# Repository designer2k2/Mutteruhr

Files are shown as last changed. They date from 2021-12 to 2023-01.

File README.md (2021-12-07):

# Mutteruhr
a pulse of alternating polarity every minute.

Motherclock, or german "Mutteruhr" is a arduino based Master Clock or german "Hauptuhr". 
It generates a short pulse of alternating polarity to drive so called slave clocks or german "Nebenuhr".

https://en.wikipedia.org/wiki/Master_clock

With a DC/DC converter it uses minimal power, the highly accurate DS3231 RTC to keep time, and a Arduino Nano Every as a Brain.

grafik

grafik

## Circuit

Schematic: https://github.com/designer2k2/Mutteruhr/blob/main/MotherClock/Motherclock%20Schematic.pdf

The actual clock drive is a transistor h-bridge, parts can be either SMD or THT. 

2 Buttons and a DIL switch is on it to make settings while the clock operates.

A small mosfet can be used to switch some LED´s on/off

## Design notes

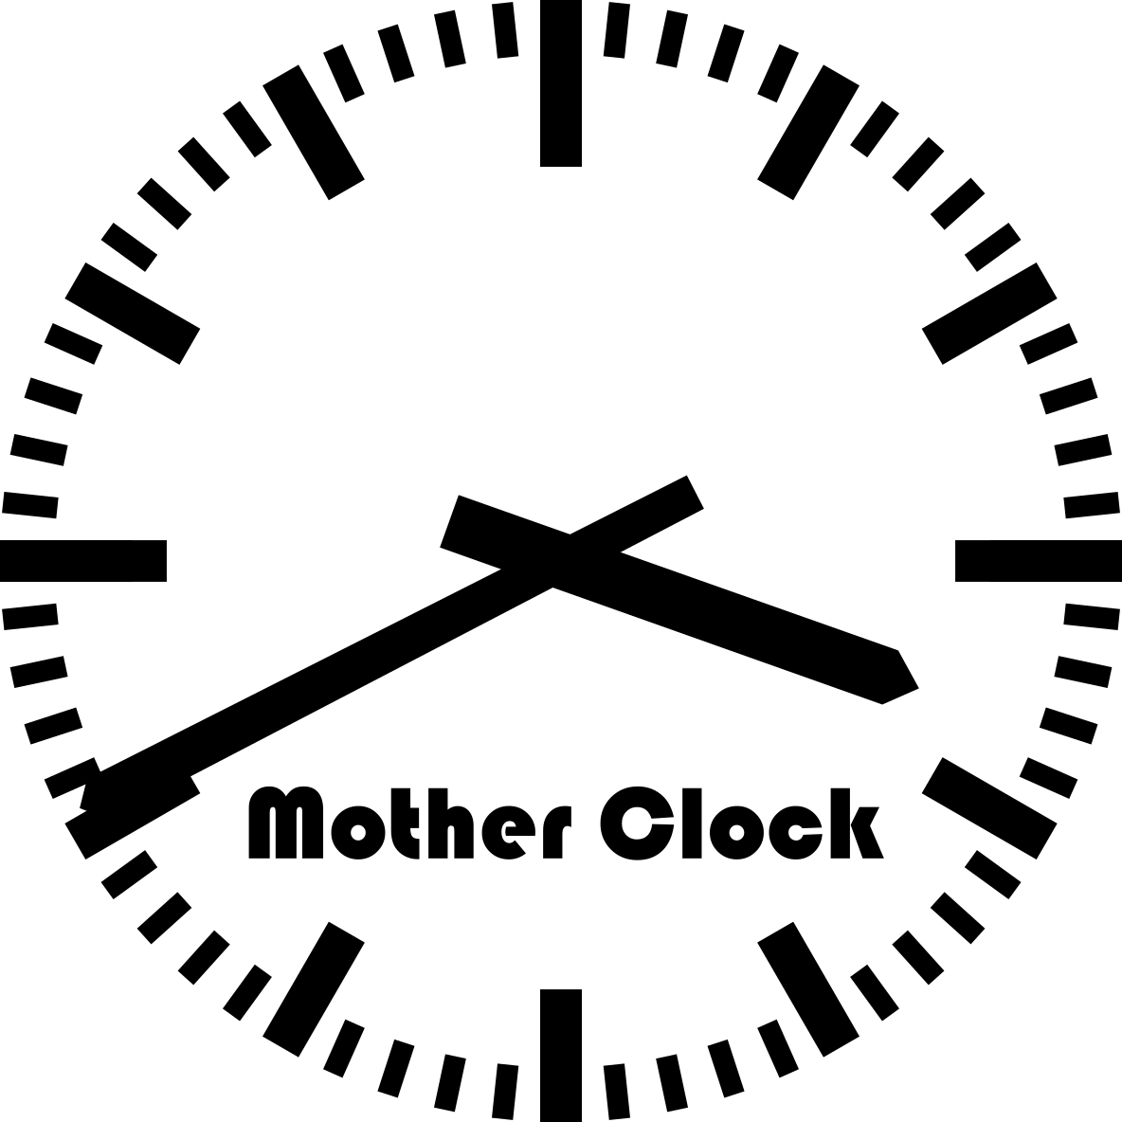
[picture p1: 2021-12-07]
MotherClock/MotherClock-brd.png

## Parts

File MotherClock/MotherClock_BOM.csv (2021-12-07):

Comment | Designator | Footprint | LCSC
Arduino_Nano_Every | A1 | Module:Arduino_Nano
1µ | C1 | Capacitor_THT:CP_Radial_D5.0mm_P2.00mm
2µ2 | C2 | Capacitor_THT:CP_Radial_D5.0mm_P2.00mm
22mF | C3 | Capacitor_THT:CP_Radial_D35.0mm_P10.00mm_SnapIn
C | C4 | Capacitor_THT:CP_Radial_D18.0mm_P7.50mm
100nF | C5,C6,C7 | Capacitor_SMD:C_0805_2012Metric
1N5818 | D1,D2,D3,D4,D6 | Diode_THT:D_DO-41_SOD81_P10.16mm_Horizontal
LED_Dual_2pin | D5 | LED_THT:LED_D3.0mm_Clear
SS15 | D7,D8,D9,D10,D11 | Diode_SMD:D_SMA
Main | J1 | TerminalBlock:TerminalBlock_Altech_AK300-4_P5.00mm
DS3231 Module | J2 | Connector_PinHeader_2.54mm:PinHeader_1x06_P2.54mm_Vertical
OLED | J3 | Connector_PinHeader_2.54mm:PinHeader_1x04_P2.54mm_Vertical
LED | J4 | TerminalBlock:TerminalBlock_Altech_AK300-2_P5.00mm
BC856 | Q1,Q3 | Package_TO_SOT_SMD:SOT-23
BC846 | Q2,Q4 | Package_TO_SOT_SMD:SOT-23
BC556 | Q5,Q7 | Package_TO_SOT_THT:TO-92_Inline_Wide
BC546 | Q6,Q8 | Package_TO_SOT_THT:TO-92_Inline_Wide
BS170 | Q9 | Package_TO_SOT_THT:TO-92_Inline
1k2 | R10 | Resistor_SMD:R_1206_3216Metric
47k | R11,R14 | Resistor_SMD:R_1206_3216Metric
10k | R12 | Resistor_SMD:R_1206_3216Metric
4k7 | R1,R2,R6,R9 | Resistor_SMD:R_1206_3216Metric
2k2 | R3,R7 | Resistor_SMD:R_1206_3216Metric
1k | R4,R5,R13 | Resistor_SMD:R_1206_3216Metric
1 | R8 | Resistor_SMD:R_1206_3216Metric
SW_DIP_x03 | SW1 | Button_Switch_THT:SW_DIP_SPSTx03_Slide_9.78x9.8mm_W7.62mm_P2.54mm
SW_Push | SW2,SW3 | Button_Switch_THT:SW_PUSH_6mm_H5mm
LM7805_TO220 | U1 | Package_TO_SOT_THT:TO-220-3_Vertical

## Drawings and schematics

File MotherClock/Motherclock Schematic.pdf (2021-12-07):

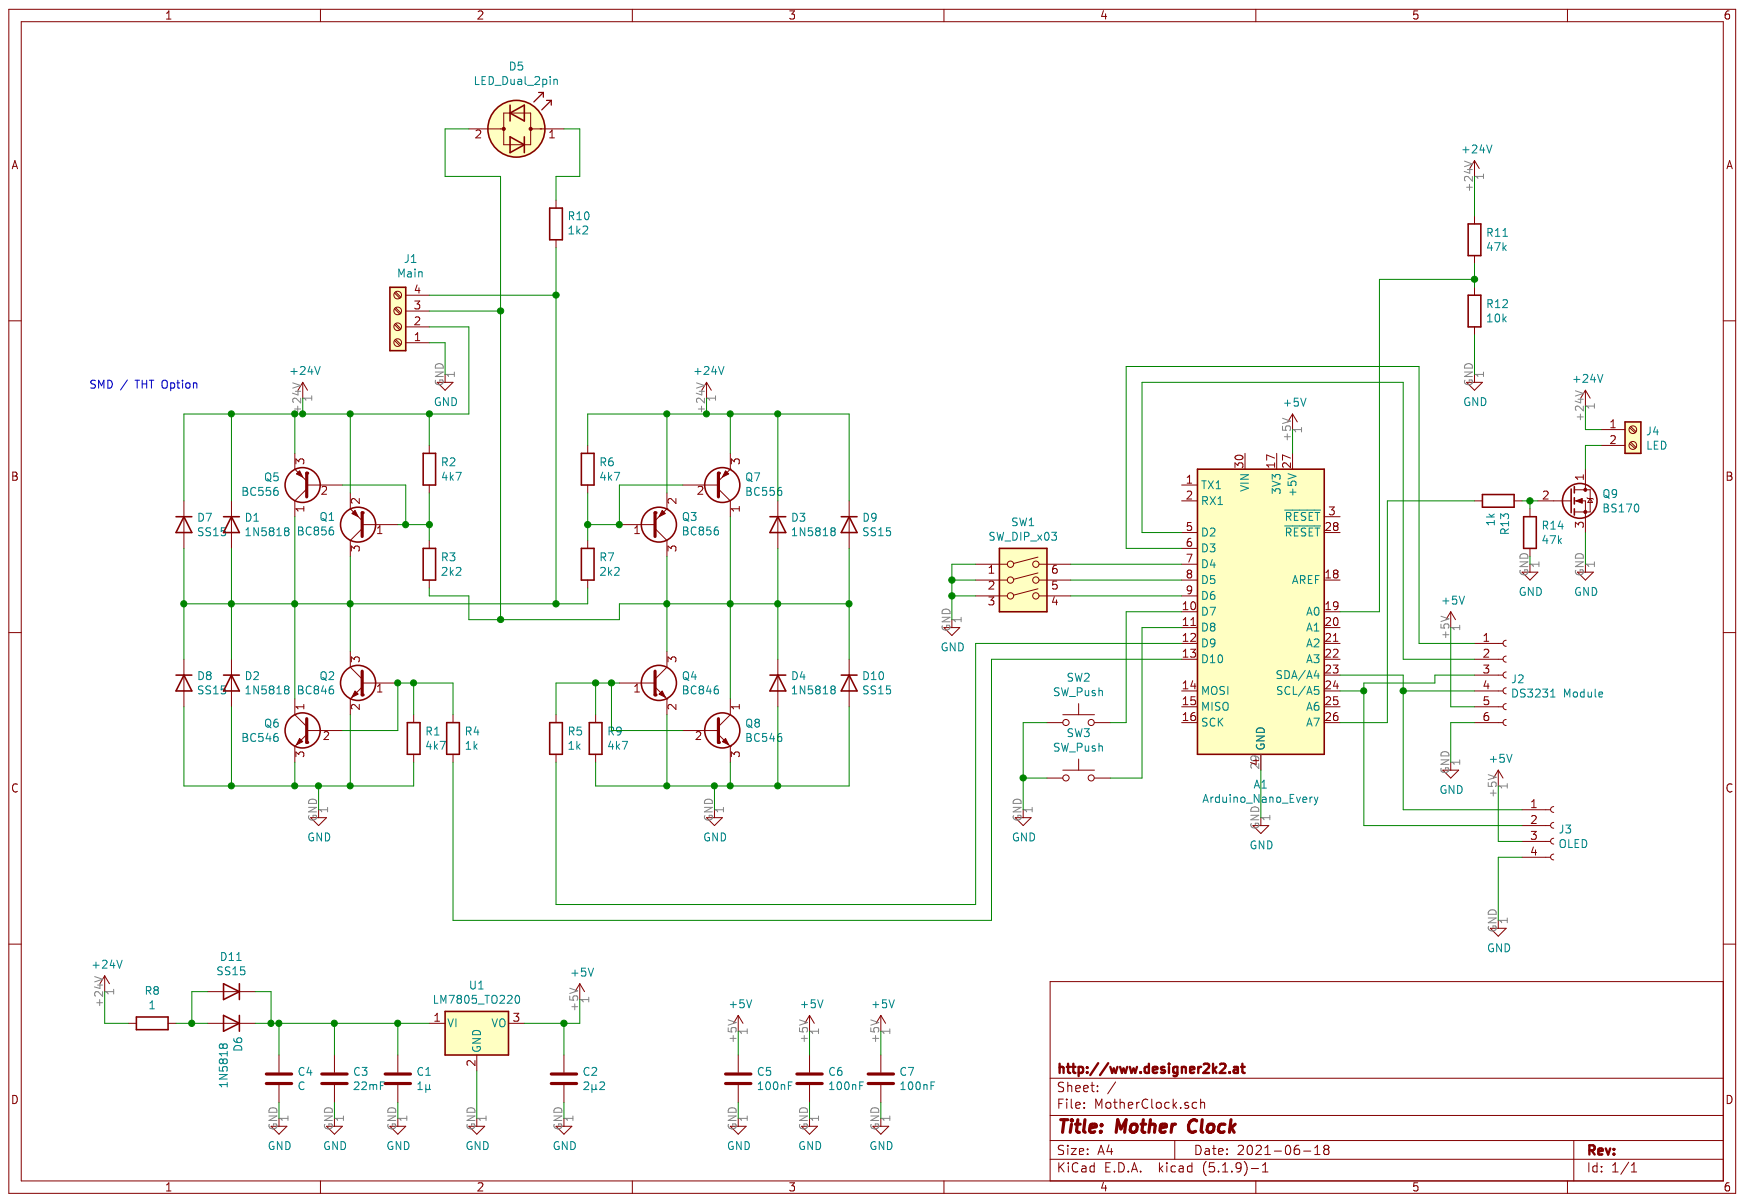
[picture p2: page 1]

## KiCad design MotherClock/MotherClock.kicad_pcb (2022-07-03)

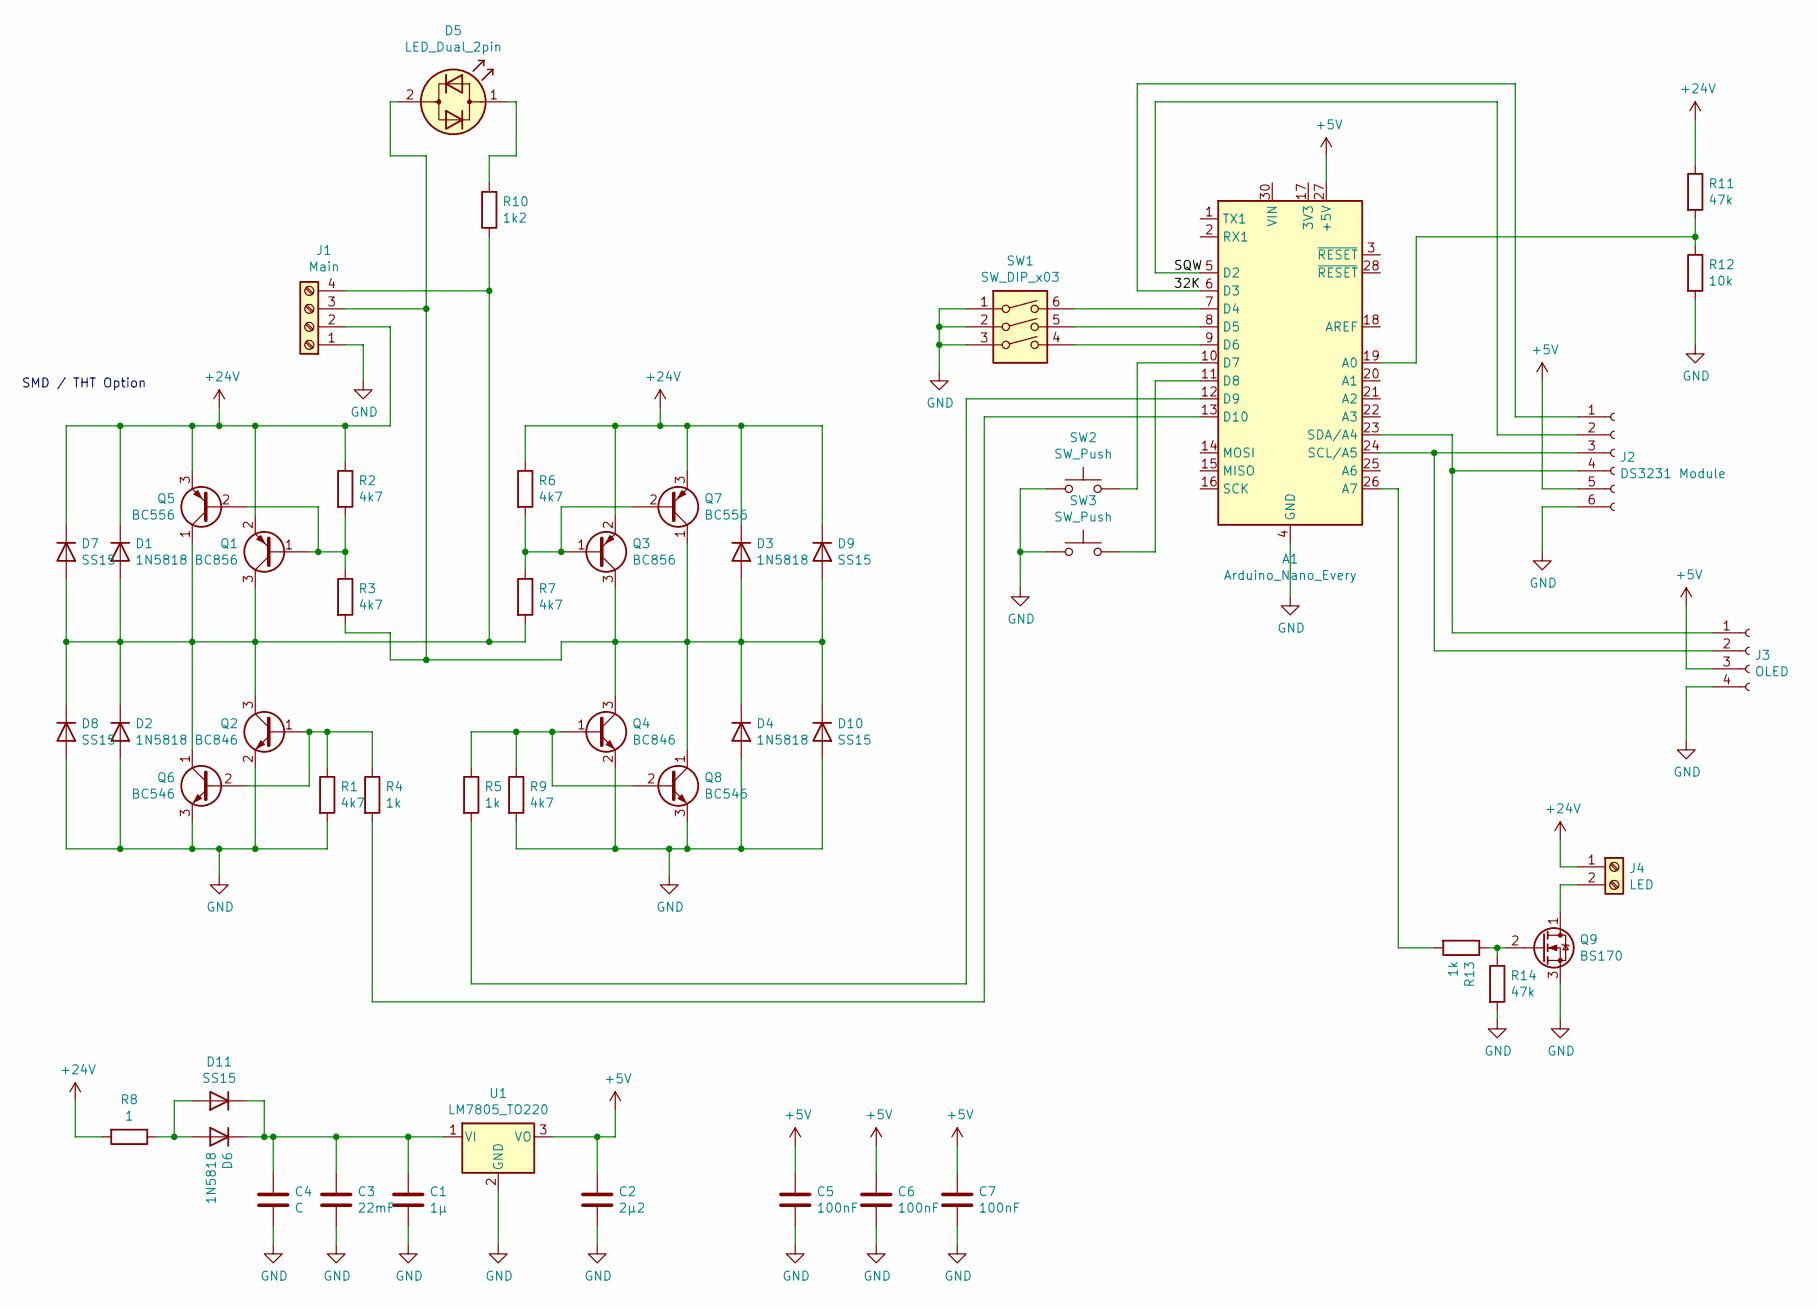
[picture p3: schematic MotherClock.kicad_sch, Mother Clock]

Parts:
A1: Arduino_Nano_Every; Arduino_Nano
C1: 1µ; CP_Radial_D5.0mm_P2.00mm
C2: 2µ2; CP_Radial_D5.0mm_P2.00mm
C3: 22mF; CP_Radial_D35.0mm_P10.00mm_SnapIn
C4: C; CP_Radial_D18.0mm_P7.50mm
C5, C6, C7: 100nF; C_0805_2012Metric
D1, D2, D3, D4, D6: 1N5818; D_DO-41_SOD81_P10.16mm_Horizontal
D5: LED_Dual_2pin; LED_D3.0mm_Clear
D7, D8, D9, D10, D11: SS15; D_SMA
J1: Main; TerminalBlock_Altech_AK300-4_P5.00mm
J2: DS3231 Module; PinHeader_1x06_P2.54mm_Vertical
J3: OLED; PinHeader_1x04_P2.54mm_Vertical
J4: LED; TerminalBlock_Altech_AK300-2_P5.00mm
Q1, Q3: BC856; SOT-23
Q2, Q4: BC846; SOT-23
Q5, Q7: BC556; TO-92_Inline_Wide
Q6, Q8: BC546; TO-92_Inline_Wide
Q9: BS170; TO-92_Inline
R1, R2, R3, R6, R7, R9: 4k7; R_1206_3216Metric
R4, R5, R13: 1k; R_1206_3216Metric
R8: 1; R_1206_3216Metric
R10: 1k2; R_1206_3216Metric
R11, R14: 47k; R_1206_3216Metric
R12: 10k; R_1206_3216Metric
SW1: SW_DIP_x03; SW_DIP_SPSTx03_Slide_9.78x9.8mm_W7.62mm_P2.54mm
SW2, SW3: SW_Push; SW_PUSH_6mm_H5mm
U1: LM7805_TO220; TO-220-3_Vertical

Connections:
+5V: A1.27 (+5V), C2.1, C5.1, C6.1, C7.1, J2.5, J3.3, U1.3 (VO)
+24V: D1.1 (K), D3.1 (K), D7.1 (K), D9.1 (K), J1.2, J4.1, Q1.2 (E), Q3.2 (E), Q5.3 (E), Q7.3 (E), R2.1, R6.1, R8.2, R11.1
GND: A1.4 (GND), A1.29 (GND), C1.2, C2.2, C3.2, C4.2, C5.2, C6.2, C7.2, D2.2 (A), D4.2 (A), D8.2 (A), D10.2 (A), J1.1, J2.6, J3.4, Q2.2 (E), Q4.2 (E), Q6.3 (E), Q8.3 (E), Q9.3 (S), R1.2, R9.2, R12.2, R14.2, SW1.1, SW1.2, SW1.3, SW2.1, SW3.1, U1.2 (GND)
unnamed: A1.5 (D2), J2.2
unnamed: A1.6 (D3), J2.1
unnamed: A1.7 (D4), SW1.6
unnamed: A1.8 (D5), SW1.5
unnamed: A1.9 (D6), SW1.4
unnamed: A1.10 (D7), SW2.2
unnamed: A1.11 (D8), SW3.2
unnamed: A1.12 (D9), R5.2
unnamed: A1.13 (D10), R4.2
unnamed: A1.19 (A0), R11.2, R12.1
unnamed: A1.23 (SDA/A4), J2.4, J3.1
unnamed: A1.24 (SCL/A5), J2.3, J3.2
unnamed: A1.26 (A7), R13.2
unnamed: C1.1, C3.1, C4.1, D6.1 (K), D11.1 (K), U1.1 (VI)
unnamed: D1.2 (A), D2.1 (K), D7.2 (A), D8.1 (K), J1.4, Q1.3 (C), Q2.3 (C), Q5.1 (C), Q6.1 (C), R7.2, R10.1
unnamed: D5.1 (KA), R10.2
unnamed: D3.2 (A), D4.1 (K), D5.2 (AK), D9.2 (A), D10.1 (K), J1.3, Q3.3 (C), Q4.3 (C), Q7.1 (C), Q8.1 (C), R3.2
unnamed: D6.2 (A), D11.2 (A), R8.1
unnamed: J4.2, Q9.1 (D)
unnamed: Q1.1 (B), Q5.2 (B), R2.2, R3.1
unnamed: Q2.1 (B), Q6.2 (B), R1.1, R4.1
unnamed: Q3.1 (B), Q7.2 (B), R6.2, R7.1
unnamed: Q4.1 (B), Q8.2 (B), R5.1, R9.1
unnamed: Q9.2 (G), R13.1, R14.1

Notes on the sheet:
SMD / THT Option

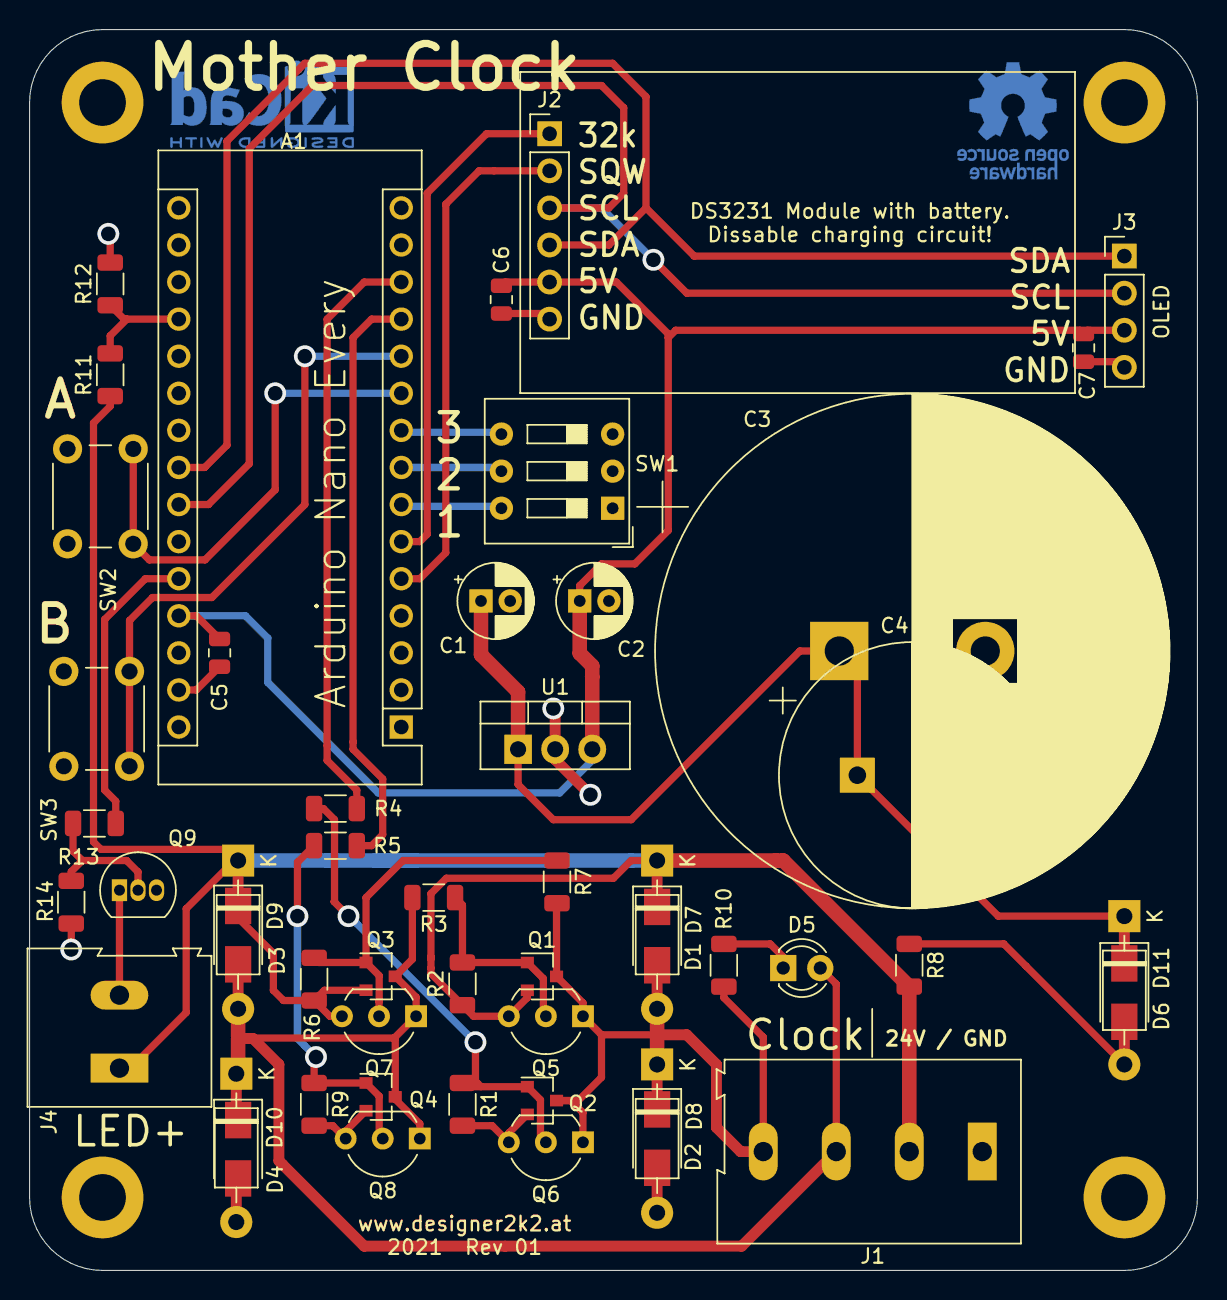
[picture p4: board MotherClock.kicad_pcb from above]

Board: 2 copper layers, 80.0 x 85.0 mm, 50 parts (0 on the bottom side), 27 nets.

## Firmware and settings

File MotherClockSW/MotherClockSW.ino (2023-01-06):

// Copyright (C) 2021 Stephan Martin <https://www.designer2k2.at>
// This file is part of Mother Clock <https://github.com/designer2k2/Mutteruhr>.
//
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
/*
   Mother Clock
   A pulse of alternating polarity every minute.

   Hardware:
     Custom PCB with mother clock circuit and 5V supply.
     Arduino Nano Every, no register emulation.
     DS3231 module with AT24C32 memory
     Optional Oled 128x64 SSD1306

   https://github.com/designer2k2/Mutteruhr

   https://www.designer2k2.at
   Stephan Martin 2021-2022
*/


/*
   Pinout description:
   Clock drive pins: D9 D10
   LED drive pin: D21 (A7)
   Input Button A: D7
   Input Button A: D8
   Switch 1: D4
   Switch 2: D5
   Switch 3: D6
   Analog 24V Input: A0 with 47k/10k divider
   DS3231 32k: D3
   DW3231 SQW: D2
   I2C SDA: A4
   I2C SCL: A5
*/


// Debug serial port:
#define DEBUG 1

#if DEBUG == 1
#define debugp(x) Serial.print(x)
#define debugln(x) Serial.println(x)
#define debugfl() Serial.flush()
#else
#define debugp(x)
#define debugln(x)
#define debugfl()
#endif


// Additional librarys
#include <DS3231.h>     // https://github.com/NorthernWidget/DS3231 (find in Library manager)
#include <Wire.h>
#include <avr/sleep.h>
#include <AT24Cxx.h>    //  https://github.com/cvmanjoo/AT24Cxx

#include <Adafruit_GFX.h>
#include <Adafruit_SSD1306.h>

#define SCREEN_WIDTH 128
#define SCREEN_HEIGHT 64
#define OLED_RESET     4
#define SCREEN_ADDRESS 0x3C
Adafruit_SSD1306 display(SCREEN_WIDTH, SCREEN_HEIGHT, &Wire, OLED_RESET);

#define memory_i2c_address 0x57
// Initilaize using AT24CXX(i2c_address, size of eeprom in KB).
AT24Cxx eep(memory_i2c_address, 32);

DS3231 myRTC;

// Parameters:
const long pulsetime = 200;            // Pulse time in milliseconds (200-800?)
const float minimumsupplyvolt = 20.0; // Minimum voltage to activate pulse

// Global variables:
bool dip1stateonpoweron = false;  // State of the DIP1 state during power up
volatile bool btogglepin = false;  //Stores the last step polarity
volatile int isrcounter = 0;  // counts up in second interval

volatile bool buttonA = false;  // the state of button A

void setup() {
  // Start the I2C interface
  Wire.begin();

  // initialize serial communications at 57600bps:
  Serial.begin(57600);
  debugln(F("MotherClock init"));

  //Set pinmodes:

  //Clockdrive:
  pinMode(9, OUTPUT);
  pinMode(10, OUTPUT);

  //Buttons / Switches / Clock Inputs:
  pinMode(2, INPUT_PULLUP);   // DS3231 SQW (1HZ)
  pinMode(3, INPUT_PULLUP);   // DW3231 32k
  pinMode(4, INPUT_PULLUP);   // DIP 1
  pinMode(5, INPUT_PULLUP);   // DIP 2
  pinMode(6, INPUT_PULLUP);   // DIP 3
  pinMode(7, INPUT_PULLUP);   // SWITCH A
  pinMode(8, INPUT_PULLUP);   // SWITCH B

  // LED output:
  pinMode(21, OUTPUT);
  pinMode(LED_BUILTIN, OUTPUT);

  // Analog input reference to VDD 5V:
  analogReference(VDD);

  // I2C Scan:
  i2c_device_scan();

  // Display:
  if (!display.begin(SSD1306_SWITCHCAPVCC, SCREEN_ADDRESS)) {
    debugln(F("SSD1306 allocation failed"));
  }
  // Clear the buffer
  display.clearDisplay();
  display.setTextSize(2);      // Normal 1:1 pixel scale
  display.setTextColor(SSD1306_WHITE); // Draw white text
  display.setCursor(0, 0);     // Start at top-left corner
  display.println(F("Motherclock ON"));
  display.display();
  delay(1000);
  // Power supply check:
  powerok();
  delay(1000);


  // DS3231 set that SQW outputs 1Hz only when power is on:
  myRTC.enableOscillator(true, false, 0);
  myRTC.enable32kHz(false);

  // Read in DIP 1 to decide the operation mode:
  dip1stateonpoweron = digitalRead(4);


  if (dip1stateonpoweron) {
    debugln("Running in interrupt mode");
    // Interrup from the DS3231 module 1Hz Signal:
    attachInterrupt(digitalPinToInterrupt(2), isr1hz, FALLING);

    // Interrupt on Button A to drive the clock manually:
    attachInterrupt(digitalPinToInterrupt(7), isrbuttonA, FALLING);
  } else {
    debugln("Running without interrupts");
  }

  // Preload the seconds from the DS3231:
  isrcounter = myRTC.getSecond();

  // Read the EEPROM to the Serial:
  debugp(F("warm "));
  debugln((int)eep.read(111));
  debugp(F("cold "));
  debugln((int)eep.read(110));
  byte buf[4];
  buf[1] = eep.read(101);
  buf[2] = eep.read(102);
  buf[3] = eep.read(103);
  buf[4] = eep.read(104);
  unsigned long var = (unsigned long)(buf[4] << 24) | (buf[3] << 16) | (buf[2] << 8) | buf[1];
  debugp(F("hours "));
  debugln(var);

  // Read the RTC Time to the Serial:
  bool century = false;
  bool h12Flag;
  bool pmFlag;
  debugp((int)myRTC.getYear());
  debugp('/');
  debugp((int)myRTC.getMonth(century));
  debugp('/');
  debugp((int)myRTC.getDate());
  debugp(' ');
  debugp((int)myRTC.getHour(h12Flag, pmFlag));
  debugp(':');
  debugp((int)myRTC.getMinute());
  debugp(':');
  debugln((int)myRTC.getSecond());
  debugfl();
}

void loop() {
  debugln(F("w"));
  debugfl();

  if (dip1stateonpoweron) {
    // Button press woke it up:
    if (buttonA) {
      pulse();
      delay(100); // delay to give the clock time to react
      //And only if the button is released reset this
      if (digitalRead(7) == HIGH) {
        buttonA = false;
        digitalWrite(LED_BUILTIN, LOW);
      }
    } else {
      // The 1Hz trigger woke it up:
      updateDisplay();
      // If the minute is full, give a pulse and reset:
      if (isrcounter >= 60) {
        isrcounter = 0;
        debugln(F("m"));
        pulse();
        minutecheck();
      }
    }

    // If button A is released go to sleep for 1 second, with the 1 second pulse from the DS3231 RTC:
    if (!buttonA) {
      enterSleep();
    }
  } else {
    // running in a sleepless mode
    if (digitalRead(7) == LOW) {
      // Button pressed, generate pulse:
      digitalWrite(LED_BUILTIN, HIGH);
      pulse();
      delay(100); // delay to give the clock time to react
      //And only if the button is released reset this
      if (digitalRead(7) == HIGH) {
        digitalWrite(LED_BUILTIN, LOW);
      }
    } else {
      // If the minute is full, give a pulse and reset:
      if (isrcounter >= 60) {
        debugln(F("m"));
        pulse();
        minutecheck();
      } else {
        delay(960);  //wait 1sec (estimated to be around 1eecond)
        isr1hz(); //increase second counter
        updateDisplay();
      }
      if (isrcounter % 5 == 0) {
        if (isrcounter >= 60) {
          debugln(F("m2"));
          pulse();
          minutecheck();
          isrcounter = myRTC.getSecond(); // sync counter from RTC
        }
      }
    }
  }
}

// Display update:
void updateDisplay()
{
  // Display the counter and current temperature:
  bool century = false;
  bool h12Flag;
  bool pmFlag;
  display.clearDisplay();
  display.setCursor(0, 0);
  display.print(F("("));
  display.print(isrcounter);
  display.println(F(")"));
  display.print(myRTC.getHour(h12Flag, pmFlag), DEC);
  display.print(F(":"));
  display.print(myRTC.getMinute(), DEC);
  display.print(F(":"));
  display.println(myRTC.getSecond(), DEC);
  display.print(myRTC.getYear(), DEC);
  display.print(F("."));
  display.print(myRTC.getMonth(century), DEC);
  display.print(F("."));
  display.println(myRTC.getDate(), DEC);
  display.print(F("T: "));
  display.print(myRTC.getTemperature(), 2);
  display.print(F(" C"));
  display.display();
}

// Sleep mode handler:
void enterSleep(void)
{
  set_sleep_mode(SLEEP_MODE_PWR_DOWN);
  sleep_enable();
  sleep_mode();
  // The program will continue from here.
  // First thing to do is disable sleep.
  sleep_disable();
}

// ISR, Button A push:
void isrbuttonA() {
  digitalWrite(LED_BUILTIN, HIGH);
  buttonA = true;
}

// ISR, this gets triggered every second by external DS3231 module:
void isr1hz() {
  isrcounter = isrcounter + 1;
}

// Check the supply voltage with the voltage divider:
bool powerok() {
  int analogin;
  float analogvolt;
  analogin = analogRead(0);
  analogvolt = (5.0 / 1024.0) * analogin;          // Vref is VDD 5.0V
  analogvolt = analogvolt * (47.0 + 10.0) / 10.0;  // Voltage divider value
  debugp(F("v: "));
  debugln(analogvolt);
  debugfl();
  display.clearDisplay();
  display.setCursor(0, 0);
  display.print(F("V: "));
  display.println(analogvolt);
  display.display();
  if (analogvolt >= minimumsupplyvolt) {
    return true;
  } else {
    return false;
  }
}

// This gives the pulse to the clock:
void pulse() {
  // First, ensure both are off:
  digitalWrite(9, false);
  digitalWrite(10, false);

  // Run only if the supply voltage is ok:
  if (!powerok()) {
    return;
  }

  // Based on old pulse decide what pin to use now:
  if (btogglepin) {
    digitalWrite(9, true);
  } else {
    digitalWrite(10, true);
  }

  // Wait the pulse time:
  delay(pulsetime);

  // all off again:
  digitalWrite(9, false);
  digitalWrite(10, false);

  // Toogle the polarity for the next run:
  btogglepin = !btogglepin;
}

// Some things to do every minute:
void minutecheck() {
  // Min Temp save to eeprom
  uint8_t actual_temp = (int) myRTC.getTemperature();
  if (eep.read(110) > actual_temp) {
    eep.write(110, actual_temp);
    debugp(F("cold "));
    debugln(actual_temp);
    debugfl();
  }
  // Max Temp:
  if (eep.read(111) < actual_temp) {
    eep.write(111, actual_temp);
    debugp(F("warm "));
    debugln(actual_temp);
    debugfl();
  }

  // hour counter increase if minute is 0
  if (myRTC.getMinute() == 0) {
    byte buf[4];
    buf[1] = eep.read(101);
    buf[2] = eep.read(102);
    buf[3] = eep.read(103);
    buf[4] = eep.read(104);
    unsigned long var = (unsigned long)(buf[4] << 24) | (buf[3] << 16) | (buf[2] << 8) | buf[1];
    var = var + 1;
    eep.update(101, (byte) var);
    eep.update(102, (byte) var >> 8);
    eep.update(103, (byte) var >> 16);
    eep.update(104, (byte) var >> 24);
    debugp(F("hours "));
    debugln(var);
    debugfl();
  }
}

// I2C Scanner, to check if all is connected:
bool i2c_device_scan() {
  byte error, address;
  bool all_ok;

  all_ok = true;

  address = memory_i2c_address;
  Wire.beginTransmission(address);
  error = Wire.endTransmission();
  if (error == 0) {
    // found memory
    debugln(F("I2C Memory found"));
  } else {
    // no memory found
    debugln(F("I2C Memory missing"));
    all_ok = false;
  }
  address = SCREEN_ADDRESS;
  Wire.beginTransmission(address);
  error = Wire.endTransmission();
  if (error == 0) {
    // found screen
    debugln(F("I2C Screen found"));
  } else {
    // no screen found
    debugln(F("I2C Screen missing"));
    all_ok = false;
  }
  address = 0x68;
  Wire.beginTransmission(address);
  error = Wire.endTransmission();
  if (error == 0) {
    // found rtc
    debugln(F("I2C RTC found"));
  } else {
    // no rtc found
    debugln(F("I2C RTC missing"));
    all_ok = false;
  }

  return all_ok;
}

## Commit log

2021-12-07 Initial fill
    PCB and software are usable
    [MotherClock-B_Cu.gbr, MotherClock-B_Mask.gbr, MotherClock-B_Paste.gbr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]
2022-06-15 Bugfix with name clock conflict
    [MotherClockSW.ino]
2022-07-03 Update PCB to KiCad 6
    [MotherClock.kicad_pcb, MotherClock.kicad_sch, MotherClock.sch]
2023-01-06 latest changes
    * begin work on additional method to run
    * working update
    DIP 1 now selects between interrupts or not (looking for a strange bug that stops the clock after some weeks)
    * add i2c scanner and improve lcd readability
    * Create spell-check.yml
    * Create compile-sketch.yml
    * Update compile-sketch.yml
    [MotherClockSW.ino]

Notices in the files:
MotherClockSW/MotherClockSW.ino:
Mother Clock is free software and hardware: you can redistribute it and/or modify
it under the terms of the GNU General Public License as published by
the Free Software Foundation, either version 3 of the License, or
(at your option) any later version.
